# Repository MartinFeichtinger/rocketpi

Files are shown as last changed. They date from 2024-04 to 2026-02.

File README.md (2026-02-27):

# RocketPi
The aim of this project is to controll a water rocket with a Raspberry Pi Zero.

## What is a water rocket?
A water rocket is a type of model rocket using water as its reaction mass.
The water is forced out by a pressurized gas, typically compressed air. Like all rocket engines, it operates on the principle of Newton's third law of motion.



## What's special about our water rocket?
The fuel tank consists of a plastic bottle. This bottle can withstand a maximum pressure of 9 bar.
In order to achieve a higher flight altitude, we have decided to strengthen this plastic bottle with fiber-reinforced tape.
Whith this new tank we are able to reach pressures up to 13 bar.
Futhermore a Raspberry Pi Zero is used to eject the parachute and determine the flight altitude.
The parachute is attached to the top of the water rocket. To eject the parachute, the pre-tensioned handle is opened with three servo motors.
-image of the water rocket

## Rocket launcher


The rocket launcher had already been built beforehand. It also allows the rocket to be filled. Two ball valves can be used to switch between water and compressed air. The water rockets can then be launched by pulling a string.

## Rocketpi


### Raspberry Pi Zero
The Raspberry Pi Zero is a tiny, affordable computer board developed by the Raspberry Pi Foundation. It's small but powerful, with features like a CPU, RAM, storage, and ports for connecting to displays and other devices. It's used for various projects like IoT, robotics, and gaming consoles due to its low cost and versatility.

### BerryIMUv4
IMU stands for Inertial Measurement Unit. It's a device that measures and reports specific forces like acceleration and angular velocity, using a combination of accelerometers, gyroscopes, and sometimes magnetometers. IMUs are commonly used in applications like navigation systems, robotics, virtual reality, and motion tracking. They provide essential data for determining an object's orientation, position, and movement in 3D space.

The BerryIMUv4 is an IMU that was specially developed for the rasberry pi zero. In addition to acceleration, rotation rate and magnetic field, it is possible to measure barometric altitude and temperature. Furthermore, there is a GPS module for position determination.

For more inforations visit: https://ozzmaker.com/product/berrygps-imu/

Example Programms: https://github.com/ozzmaker/BerryIMU

### Power Board
The power board connects the Raspberry Pi to the lithium battery and the servo motors. It also acts as a bridge between the Raspberry Pi and the BerryIMUv4 sensor module, and between the Raspberry Pi and the control panel.

#### Schematic
Screenshot From 2026-02-27 09-51-35

#### PCB layout
Screenshot From 2026-02-27 09-52-22

### Controll Panel
The control panel enables interaction with the Raspberry Pi. On the one hand, control signals can be sent to the Raspberry Pi via a button, and on the other hand, the status of the Raspberry Pi can be displayed via LEDs. The entire system is switched on with a power switch. To signal that the Raspberry Pi is booting, a flashing signal is generated via a 555 timer. Immediately after the boot process, the reset input of the 555 timer is triggered and the boot LED stops flashing and remains lit. 

#### Schematic
Screenshot From 2026-02-27 09-53-32

#### PCB layout
Screenshot From 2026-02-27 09-59-49

## Software
### State-Machine
stateMachine

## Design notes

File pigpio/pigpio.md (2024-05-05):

# pigpio
For all further C programms we will use the `pigpiod_if2.h` library to controll the GPIO-Pins of the Raspberry Pi.
This library allow to control the GPIOs via the socket interface to the pigpio daemon.

To be able to use this library and program the GPIO-Pins, the pigpio package must be installed as explained in the setup guild.

For more informations about pigpio: https://abyz.me.uk/rpi/pigpio/index.html

## GPIO-Pinout
GPIO-Pinout-Diagram-2

## Test program
To test if the pigpio library is installed correctly you can use the `pigpioTest.c` programm.
This programm will toggle the GPIO 17 between HIGH and LOW. 
To make this visible you can use a led with a resistor connected to ground.

- build up the test schematic
- compile the test programm `gcc -Wall -pthread -o pigpioTest pigpioTest.c -lpigpiod_if2 -lrt`
- run the programm with `./pigpioTest`

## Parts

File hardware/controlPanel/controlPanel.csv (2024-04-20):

Source: | /home/martin/Otelo/Elektroniknode/Wasserrakete/Schaltplan/fallschirmsystem_bedienfeld/fallschirmsystem_bedienfeld.kicad_sch
Date: | Fr 09 Dez 2022 00:26:18
Tool: | Eeschema 6.0.9-8da3e8f707~117~ubuntu20.04.1
Generator: | /usr/share/kicad/plugins/bom_csv_grouped_by_value.py
Component Count: | 15
Individual Components:
Item | Qty | Reference(s) | Value | LibPart | Footprint | Datasheet
 |  | C1 | 10u | Device:C | Capacitor_SMD:C_0805_2012Metric_Pad1.18x1.45mm_HandSolder | ~
 |  | D1 | D_Schottky | Device:D_Schottky | Diode_SMD:D_SMA_Handsoldering | ~
 |  | D2 | D_Schottky | Device:D_Schottky | Diode_SMD:D_SMA_Handsoldering | ~
 |  | D3 | Boot_LED | Device:LED | LED_THT:LED_D5.0mm_Horizontal_O1.27mm_Z3.0mm | ~
 |  | D4 | GPS_LED | Device:LED | LED_THT:LED_D5.0mm_Horizontal_O1.27mm_Z3.0mm | ~
 |  | D5 | Network_LED | Device:LED | LED_THT:LED_D5.0mm_Horizontal_O1.27mm_Z3.0mm | ~
 |  | J1 | Power Supply | Connector:Conn_01x02_Female | Connector_Molex:Molex_Micro-Latch_53253-0270_1x02_P2.00mm_Vertical | ~
 |  | J2 | Conn_01x06_Female | Connector:Conn_01x06_Female | Connector_Molex:Molex_KK-254_AE-6410-06A_1x06_P2.54mm_Vertical | ~
 |  | R1 | 10k | Device:R | Resistor_SMD:R_0805_2012Metric_Pad1.20x1.40mm_HandSolder | ~
 |  | R2 | 68k | Device:R | Resistor_SMD:R_0805_2012Metric_Pad1.20x1.40mm_HandSolder | ~
 |  | R3 | 220 | Device:R | Resistor_SMD:R_0805_2012Metric_Pad1.20x1.40mm_HandSolder | ~
 |  | R4 | 680 | Device:R | Resistor_SMD:R_0805_2012Metric_Pad1.20x1.40mm_HandSolder | ~
 |  | R5 | 220 | Device:R | Resistor_SMD:R_0805_2012Metric_Pad1.20x1.40mm_HandSolder | ~
 |  | SW1 | Ein/Aus | Switch:SW_Push_SPDT | footprints:slide_switch | ~
 |  | U1 | LM555xM | Timer:LM555xM | Package_DIP:DIP-8_W7.62mm_Socket_LongPads | http://www.ti.com/lit/ds/symlink/lm555.pdf
Collated Components:
Item | Qty | Reference(s) | Value | LibPart | Footprint | Datasheet
1 | 1 | C1 | 10u | Device:C | Capacitor_SMD:C_0805_2012Metric_Pad1.18x1.45mm_HandSolder | ~
2 | 2 | D1, D2 | D_Schottky | Device:D_Schottky | Diode_SMD:D_SMA_Handsoldering | ~
3 | 1 | D3 | Boot_LED | Device:LED | LED_THT:LED_D5.0mm_Horizontal_O1.27mm_Z3.0mm | ~
4 | 1 | D4 | GPS_LED | Device:LED | LED_THT:LED_D5.0mm_Horizontal_O1.27mm_Z3.0mm | ~
5 | 1 | D5 | Network_LED | Device:LED | LED_THT:LED_D5.0mm_Horizontal_O1.27mm_Z3.0mm | ~
6 | 1 | J1 | Power Supply | Connector:Conn_01x02_Female | Connector_Molex:Molex_Micro-Latch_53253-0270_1x02_P2.00mm_Vertical | ~
7 | 1 | J2 | Conn_01x06_Female | Connector:Conn_01x06_Female | Connector_Molex:Molex_KK-254_AE-6410-06A_1x06_P2.54mm_Vertical | ~
8 | 1 | R1 | 10k | Device:R | Resistor_SMD:R_0805_2012Metric_Pad1.20x1.40mm_HandSolder | ~
9 | 1 | R2 | 68k | Device:R | Resistor_SMD:R_0805_2012Metric_Pad1.20x1.40mm_HandSolder | ~
10 | 2 | R3, R5 | 220 | Device:R | Resistor_SMD:R_0805_2012Metric_Pad1.20x1.40mm_HandSolder | ~
11 | 1 | R4 | 680 | Device:R | Resistor_SMD:R_0805_2012Metric_Pad1.20x1.40mm_HandSolder | ~
12 | 1 | SW1 | Ein/Aus | Switch:SW_Push_SPDT | footprints:slide_switch | ~
13 | 1 | U1 | LM555xM | Timer:LM555xM | Package_DIP:DIP-8_W7.62mm_Socket_LongPads | http://www.ti.com/lit/ds/symlink/lm555.pdf

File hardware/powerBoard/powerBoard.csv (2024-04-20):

Source: | /home/martin/Otelo/Elektroniknode/Wasserrakete/Schaltplan/power_board/power_board.kicad_sch
Date: | Sa 12 Aug 2023 21:56:18
Tool: | Eeschema 6.0.10-86aedd382b~118~ubuntu22.10.1
Generator: | /usr/share/kicad/plugins/bom_csv_grouped_by_value_with_fp.py
Component Count: | 25
Ref | Qnty | Value | Cmp name | Footprint | Description | Vendor
C1, C2, | 2 | 100nF | C | Capacitor_SMD:C_0805_2012Metric_Pad1.18x1.45mm_HandSolder | Unpolarized capacitor
C3, C4, C5, C6, C7, C8, | 6 | 10u | C | Capacitor_SMD:C_0805_2012Metric_Pad1.18x1.45mm_HandSolder | Unpolarized capacitor
J1, | 1 | Batt | Conn_01x02_Female | MyFootprints:Pfusch_Conn | Generic connector, single row, 01x02, script generated (kicad-library-utils/schlib/autogen/connector/)
J2, | 1 | Berry IMU | Conn_02x05_Odd_Even | Connector_PinSocket_2.54mm:PinSocket_2x05_P2.54mm_Vertical | Generic connector, double row, 02x05, odd/even pin numbering scheme (row 1 odd numbers, row 2 even numbers), script generated (kicad-library-utils/schlib/autogen/connector/)
J3, | 1 | Control_Panel | Conn_02x04_Top_Bottom | Connector_PinHeader_2.54mm:PinHeader_2x04_P2.54mm_Vertical | Generic connector, double row, 02x04, top/bottom pin numbering scheme (row 1: 1...pins_per_row, row2: pins_per_row+1 ... num_pins), script generated (kicad-library-utils/schlib/autogen/connector/)
J4, | 1 | Servo_1 | Conn_01x02_Female | MyFootprints:Pfusch_Conn | Generic connector, single row, 01x02, script generated (kicad-library-utils/schlib/autogen/connector/)
J5, | 1 | Servo_2 | Conn_01x02_Female | MyFootprints:Pfusch_Conn | Generic connector, single row, 01x02, script generated (kicad-library-utils/schlib/autogen/connector/)
J6, | 1 | Servo_3 | Conn_01x02_Female | MyFootprints:Pfusch_Conn | Generic connector, single row, 01x02, script generated (kicad-library-utils/schlib/autogen/connector/)
J7, | 1 | Raspi | Conn_02x05_Odd_Even | Connector_PinSocket_2.54mm:PinSocket_2x05_P2.54mm_Vertical | Generic connector, double row, 02x05, odd/even pin numbering scheme (row 1 odd numbers, row 2 even numbers), script generated (kicad-library-utils/schlib/autogen/connector/)
J8, | 1 | Masse | Conn_01x02_Male | Connector_PinHeader_2.54mm:PinHeader_1x02_P2.54mm_Vertical | Generic connector, single row, 01x02, script generated (kicad-library-utils/schlib/autogen/connector/)
R1, R2, R3, | 3 | 10k | R | Resistor_SMD:R_0805_2012Metric_Pad1.20x1.40mm_HandSolder | Resistor
R4, R5, | 2 | 4,7k | R | Resistor_SMD:R_0805_2012Metric_Pad1.20x1.40mm_HandSolder | Resistor
R6, R7, | 2 | R | R | Resistor_SMD:R_0805_2012Metric_Pad1.20x1.40mm_HandSolder | Resistor
U1, | 1 | R-78C5.0-1.0 | R-78C5.0-1.0 | Converter_DCDC:Converter_DCDC_RECOM_R-78E-0.5_THT | 1A Step-Down DC/DC-Regulator, 7-42V input, 5V fixed Output Voltage, LM78xx replacement, -40°C to +85°C, SIP3
U2, | 1 | DRV8801PWP | DRV8801PWP | Package_SO:HTSSOP-16-1EP_4.4x5mm_P0.65mm_EP3.4x5mm_Mask3x3mm_ThermalVias | H-Bridge Motor Driver, TSSOP-16

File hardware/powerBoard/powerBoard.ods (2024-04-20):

Component Count: | 25
Ref | Qnty | Value
C1, C2, | 2 | 100nF
C3, C4, C5, C6, C7, C8, | 6 | 10u
J1, | 1 | Batt
J2, | 1 | Berry IMU
J3, | 1 | Control_Panel
J4, | 1 | Servo_1
J5, | 1 | Servo_2
J6, | 1 | Servo_3
J7, | 1 | Raspi
J8, | 1 | Masse
R1, R2, R3, | 3 | 10k
R4, R5, | 2 | 4,7k
R6, R7, | 2 | R
U1, | 1 | R-78C5.0-1.0
U2, | 1 | DRV8801PWP

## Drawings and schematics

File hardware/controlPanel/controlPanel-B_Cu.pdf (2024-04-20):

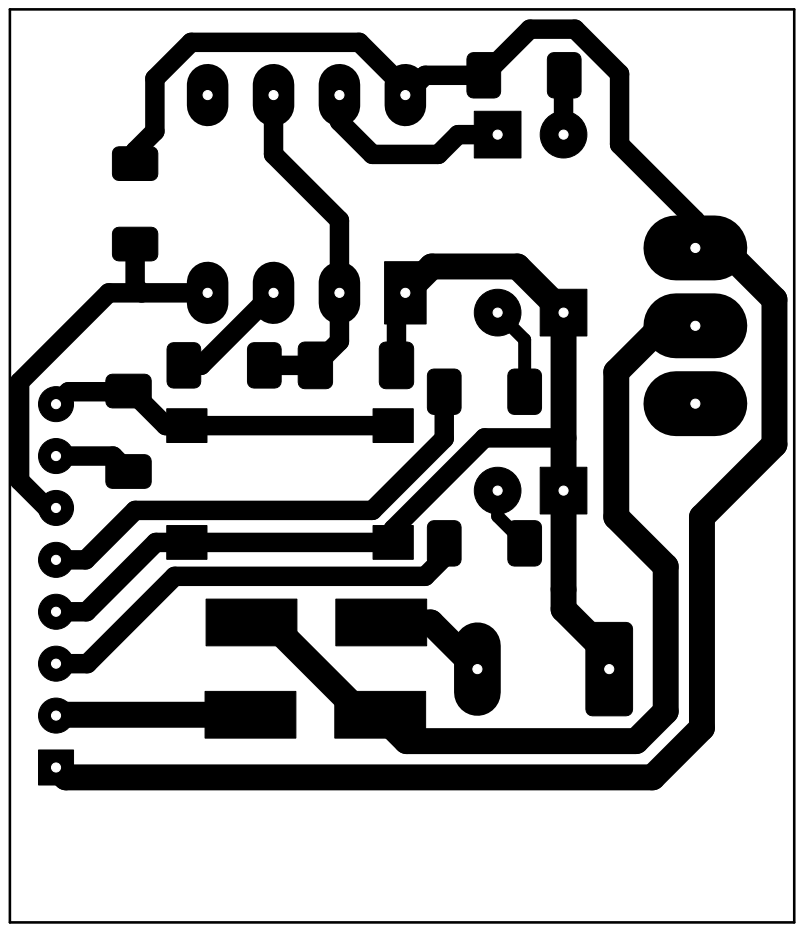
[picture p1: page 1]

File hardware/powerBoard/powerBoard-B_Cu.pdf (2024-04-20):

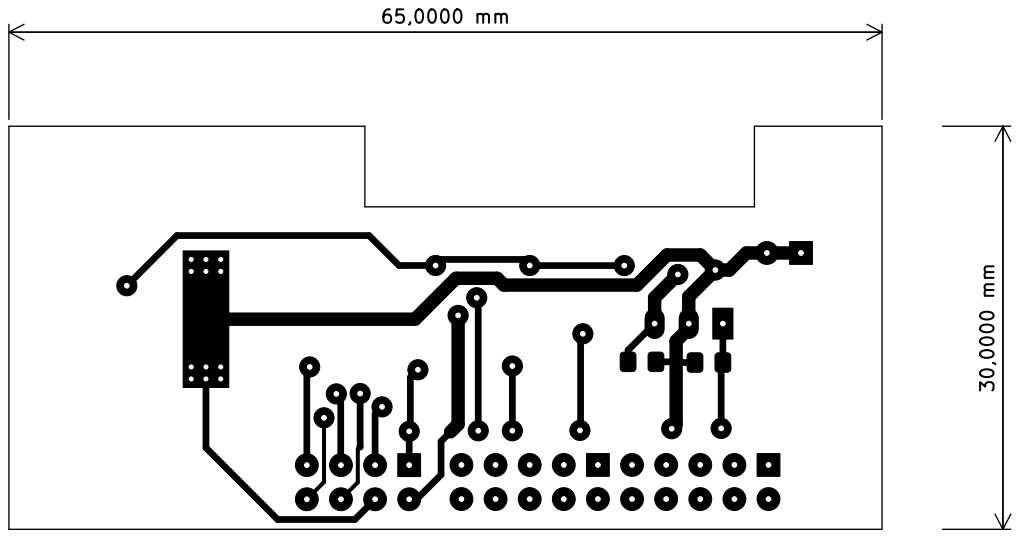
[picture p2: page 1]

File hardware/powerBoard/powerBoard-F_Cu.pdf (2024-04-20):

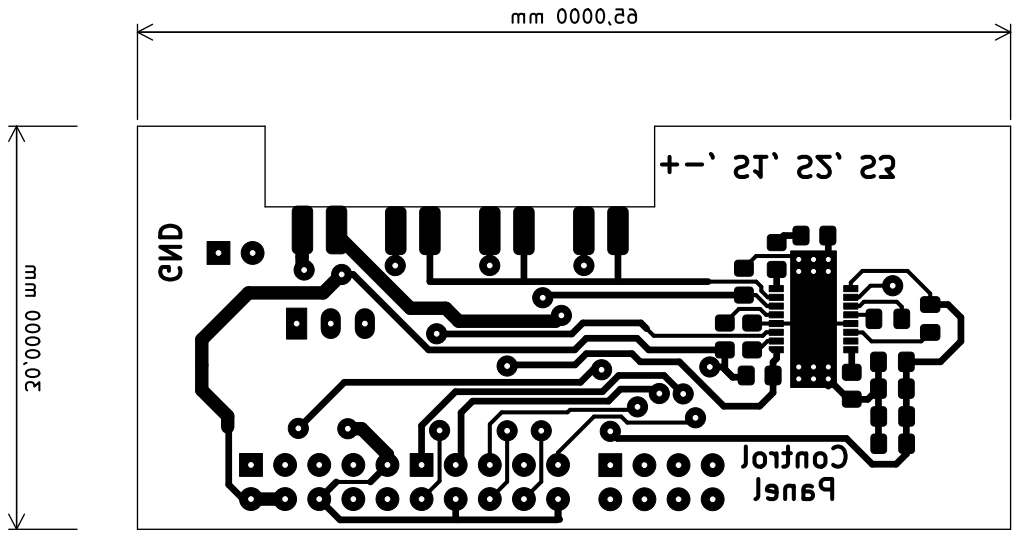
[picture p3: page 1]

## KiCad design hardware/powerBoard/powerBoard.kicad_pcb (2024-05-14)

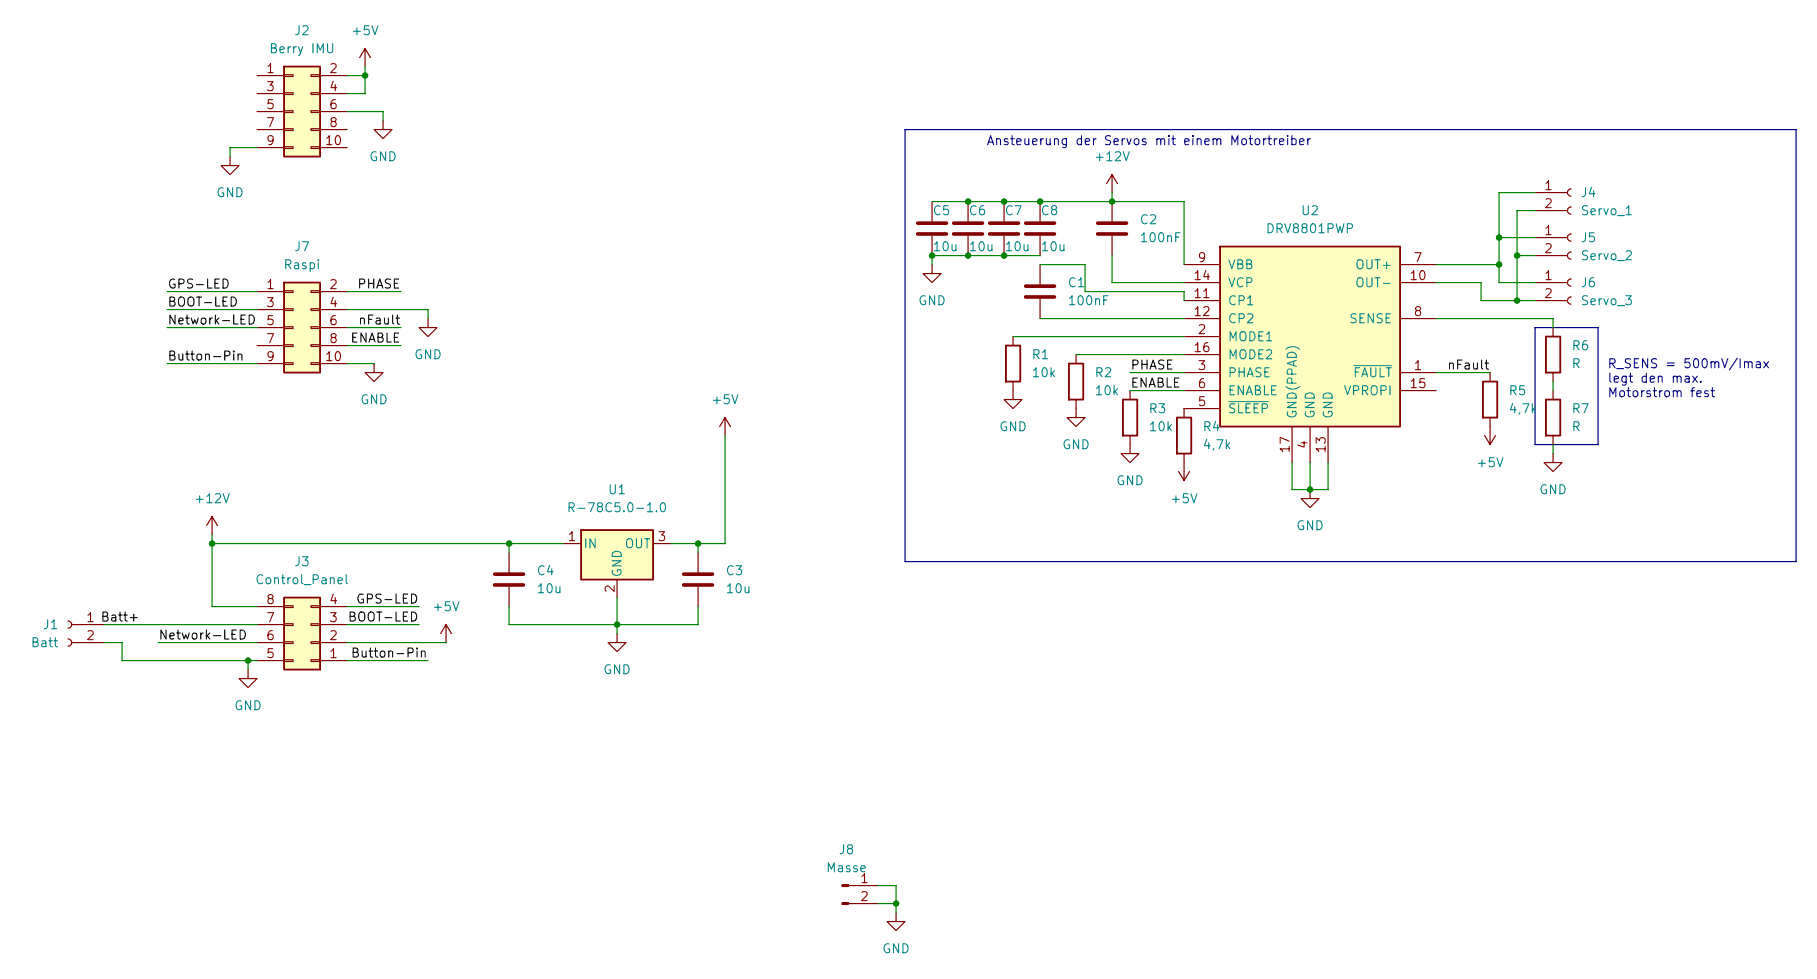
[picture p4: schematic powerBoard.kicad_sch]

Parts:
C1, C2: 100nF; C_0805_2012Metric_Pad1.18x1.45mm_HandSolder
C3, C4, C5, C6, C7, C8: 10u; C_0805_2012Metric_Pad1.18x1.45mm_HandSolder
J1: Batt; Pfusch_Conn
J2: Berry IMU; PinSocket_2x05_P2.54mm_Vertical
J3: Control_Panel; IDC-Header_2x04_P2.54mm_Vertical
J4: Servo_1; Pfusch_Conn
J5: Servo_2; Pfusch_Conn
J6: Servo_3; Pfusch_Conn
J7: Raspi; PinSocket_2x05_P2.54mm_Vertical
J8: Masse; PinHeader_1x02_P2.54mm_Vertical
R1, R2, R3: 10k; R_0805_2012Metric_Pad1.20x1.40mm_HandSolder
R4, R5: 4,7k; R_0805_2012Metric_Pad1.20x1.40mm_HandSolder
R6, R7: R; R_0805_2012Metric_Pad1.20x1.40mm_HandSolder
U1: R-78C5.0-1.0; Converter_DCDC_RECOM_R-78E-0.5_THT
U2: DRV8801PWP; HTSSOP-16-1EP_4.4x5mm_P0.65mm_EP3.4x5mm_Mask3x3mm_ThermalVi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

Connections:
+5V: C3.1, J2.2, J2.4, J3.2, R4.2, R5.2, U1.3 (OUT); also elsewhere on the board
+12V: C2.1, C4.1, C5.1, C6.1, C7.1, C8.1, J3.8, U1.1 (IN), U2.9 (VBB)
/BOOT-LED: J3.3, J7.3
/Batt+: J1.1, J3.7
/Button-Pin: J3.1, J7.9
/ENABLE: J7.8, R3.1, U2.6 (ENABLE)
/GPS-LED: J3.4, J7.1
/Network-LED: J3.6, J7.5
/PHASE: J7.2, U2.3 (PHASE)
/nFault: J7.6, R5.1, U2.1 (~FAULT)
GND: C3.2, C4.2, C5.2, C6.2, C7.2, C8.2, J1.2, J2.6, J2.9, J3.5, J7.4, J7.10, J8.1, J8.2, R1.2, R2.2, R3.2, R7.2, U1.2 (GND), U2.4 (GND), U2.13 (GND), U2.17 (GND(PPAD)); also elsewhere on the board
unnamed: C1.1, U2.11 (CP1)
unnamed: C1.2, U2.12 (CP2)
unnamed: C2.2, U2.14 (VCP)
unnamed: J4.1, J5.1, J6.1, U2.7 (OUT+)
unnamed: J4.2, J5.2, J6.2, U2.10 (OUT-)
unnamed: R1.1, U2.2 (MODE1)
unnamed: R2.1, U2.16 (MODE2)
unnamed: R4.1, U2.5 (~SLEEP)
unnamed: R6.1, U2.8 (SENSE)
unnamed: R6.2, R7.1

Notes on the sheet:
R_SENS = 500mV/Imax legt den max. Motorstrom fest
Ansteuerung der Servos mit einem Motortreiber

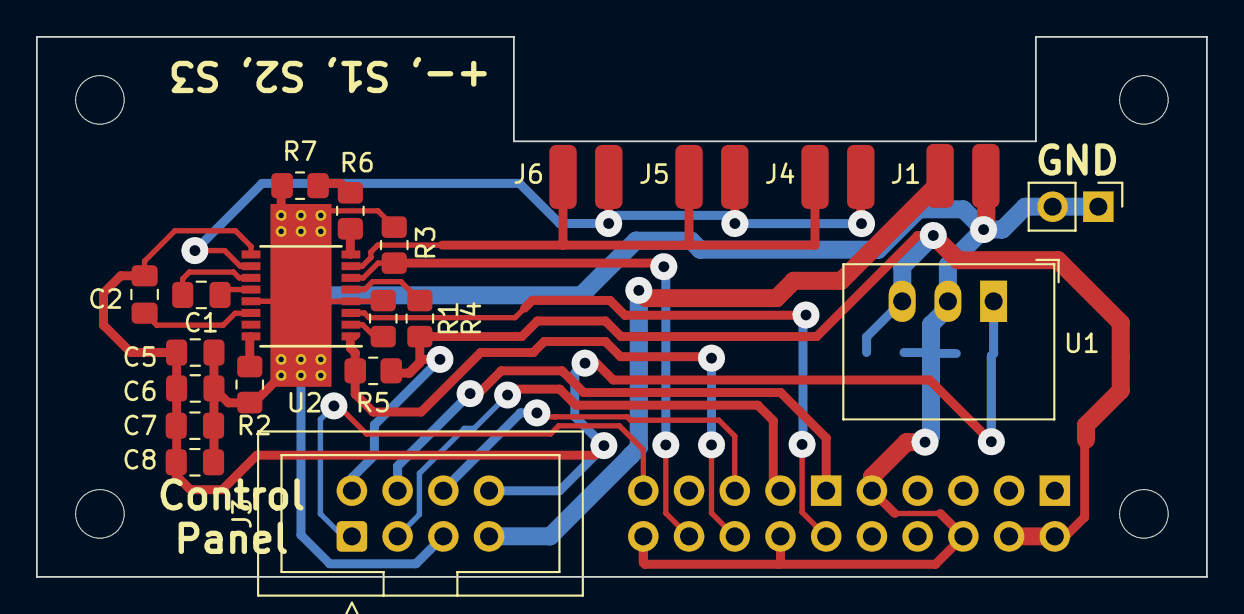
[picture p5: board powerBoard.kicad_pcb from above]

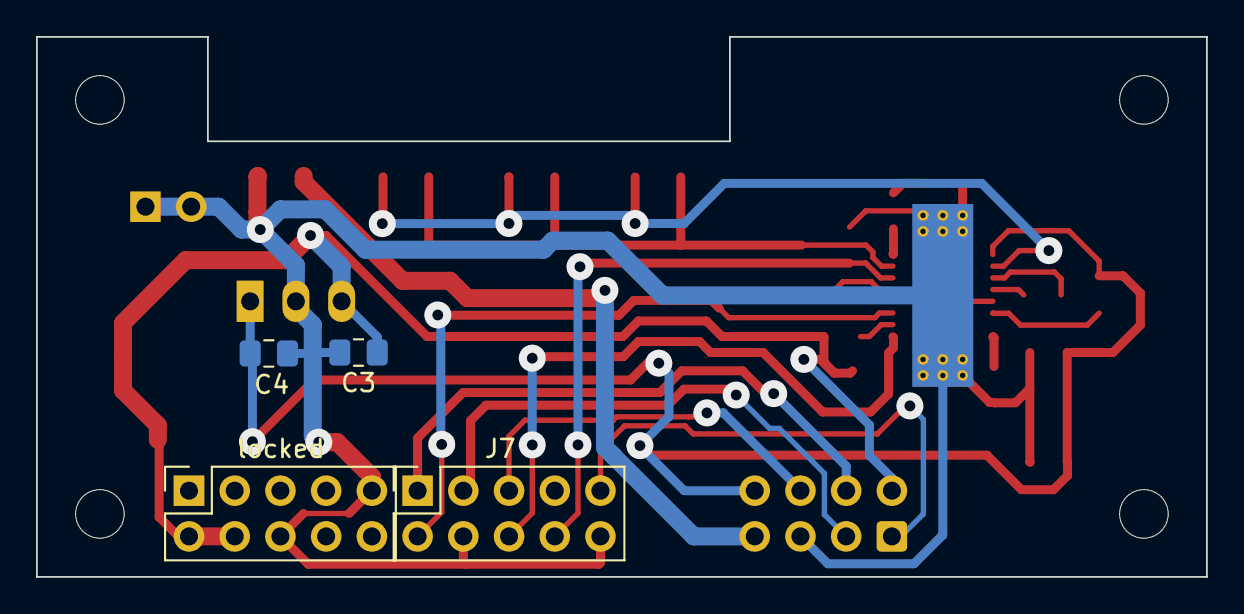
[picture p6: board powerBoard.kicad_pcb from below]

Board: 2 copper layers, 65.0 x 30.0 mm, 25 parts (4 on the bottom side), 21 nets.

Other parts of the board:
locked: Berry IMU; PinSocket_2x05_P2.54mm_Vertical

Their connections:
+5V: locked.2, locked.4; also elsewhere on the board
GND: locked.6, locked.9; also elsewhere on the board

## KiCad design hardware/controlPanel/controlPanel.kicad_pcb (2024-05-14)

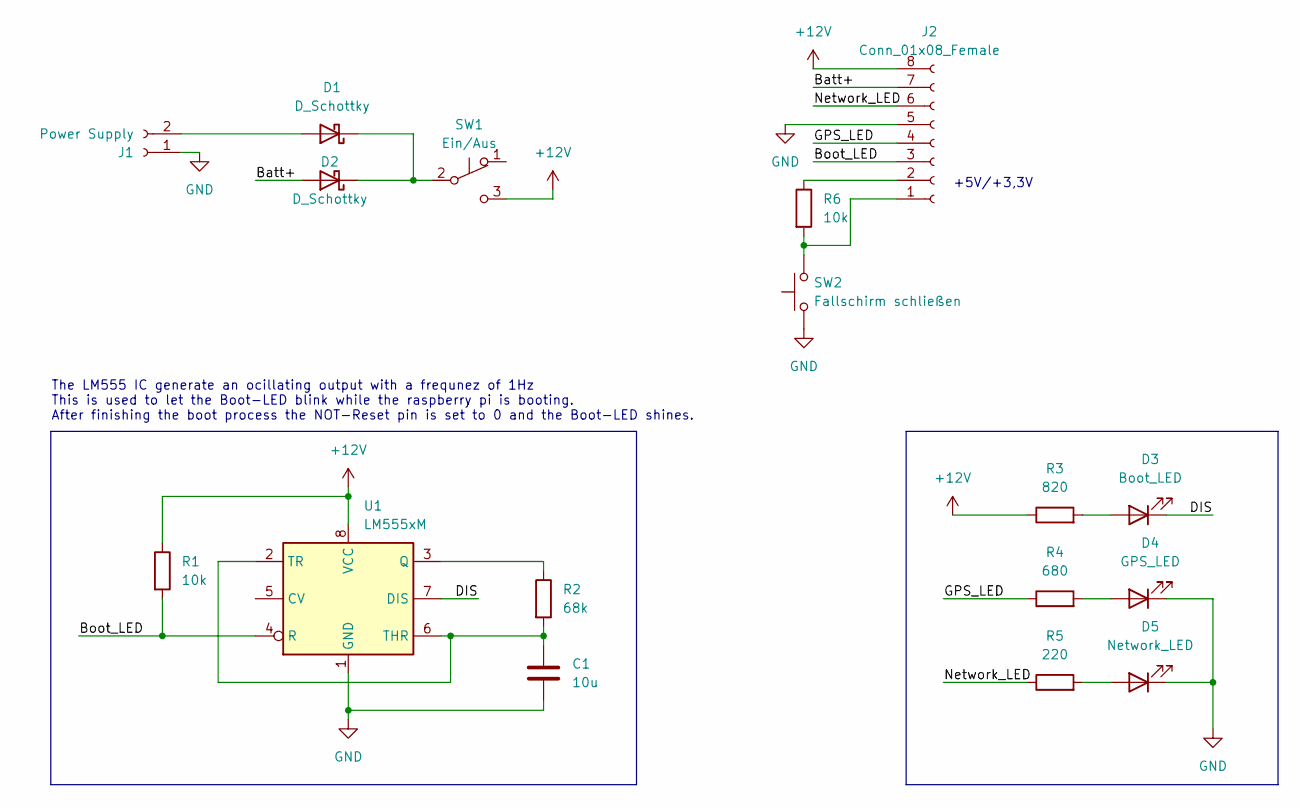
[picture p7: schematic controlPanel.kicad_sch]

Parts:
C1: 10u; C_1206_3216Metric_Pad1.33x1.80mm_HandSolder
D1, D2: D_Schottky; D_SMA_Handsoldering
D3: Boot_LED; LED_D3.0mm
D4: GPS_LED; LED_D3.0mm
D5: Network_LED; LED_D3.0mm
J1: Power Supply; PhoenixContact_MCV_1,5_2-G-5.08_1x02_P5.08mm_Vertical
J2: Conn_01x08_Female; PinHeader_1x08_P2.00mm_Vertical
R1, R6: 10k; R_1206_3216Metric_Pad1.30x1.75mm_HandSolder
R2: 68k; R_1206_3216Metric_Pad1.30x1.75mm_HandSolder
R3: 820; R_1206_3216Metric_Pad1.30x1.75mm_HandSolder
R4: 680; R_1206_3216Metric_Pad1.30x1.75mm_HandSolder
R5: 220; R_1206_3216Metric_Pad1.30x1.75mm_HandSolder
SW1: Ein/Aus; slide_switch
SW2: Fallschirm schließen; SW_Push_1P1T_NO_6x6mm_H9.5mm
U1: LM555xM; DIP-8_W7.62mm_Socket_LongPads

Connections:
+12V: J2.8, R1.1, R3.1, SW1.3 (C), U1.8 (VCC)
/Batt+: D2.2 (A), J2.7
/Boot_LED: J2.3, R1.2, U1.4 (R)
/DIS: D3.1 (K), U1.7 (DIS)
/GPS_LED: J2.4, R4.1
/Network_LED: J2.6, R5.1
GND: C1.2, D4.1 (K), D5.1 (K), J1.1, J2.5, SW2.1, U1.1 (GND)
unnamed: C1.1, R2.2, U1.2 (TR), U1.6 (THR)
unnamed: D1.1 (K), D2.1 (K), SW1.2 (B)
unnamed: D1.2 (A), J1.2
unnamed: D3.2 (A), R3.2
unnamed: D4.2 (A), R4.2
unnamed: D5.2 (A), R5.2
unnamed: J2.1, R6.2, SW2.2
unnamed: J2.2, R6.1
unnamed: R2.1, U1.3 (Q)

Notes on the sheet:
+5V/+3,3V
The LM555 IC generate an ocillating output with a frequnez of 1Hz This is used to let the Boot-LED blink while the raspberry pi is booting. After finishing the boot process the NOT-Reset pin is set to 0 and the Boot-LED shines.

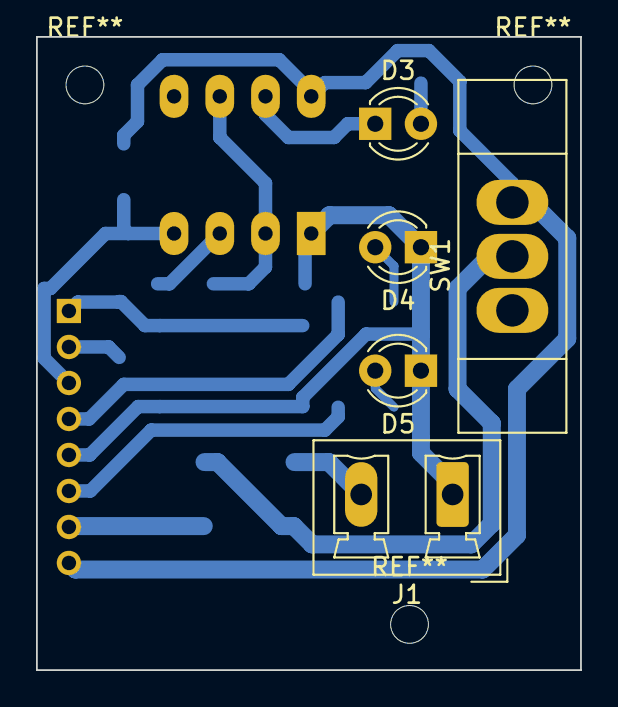
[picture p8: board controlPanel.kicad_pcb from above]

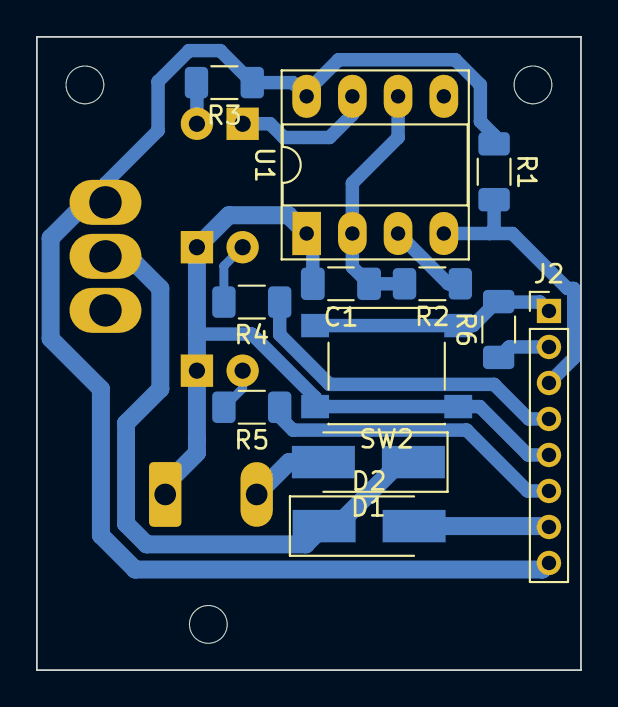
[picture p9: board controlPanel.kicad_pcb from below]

Board: 2 copper layers, 30.2 x 35.2 mm, 17 parts (12 on the bottom side), 16 nets.

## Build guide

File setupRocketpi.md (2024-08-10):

# Setup your Rocketpi
This projekt is developed for a **Raspberry Pi Zero 2W**. You can also use an Raspberry Pi Zero W but the *Remote Development Extenion* for VS-Code won't work.

## Prepare Raspberry Pi
- install the Raspberry Pi imager (`sudo apt install rpi-imager`)
- insert your microSD-Card (at least 8GB)
- open and choose **Raspberry Pi OS Lite (64-Bit)** for the **Raspberry Pi Zero 2W** (32-Bit  for Raspberry Pi Zero W)
- select your microSD-Card and write your image

## First Boot
- insert your microSD-Card in your Raspberry Zero 2W
- connect the Raspberry Pi to a monitor, a keyboard and powersupply and let him boot
- open the `raspi-config` and change hostname to `rocketpi-xx`  
- and activate `ssh`
- activate wlan (mobile HotSpot rescommended) and reboot
- (the order of this settings are important)

## Further configurations
- connect to the Raspi via ssh (`ssh pi@rocketpi-xx.local`) 
- open `raspi-config` and activate `i2c` and `Serial`
- change the time zone to your local time. (you can check the time with the comand `date`)
- close `raspi-config` and reboot

## Clone Rocketpi-Projekt
- install git: `sudo apt install git`
- `git clone https://github.com/MartinFeichtinger/rocketpi`
- bei Änderungen mit `git commit` und `git push` hochladen (username and token erforderlich)

## Configurations for the GPIO-Programming
- install the pigpio library `sudo apt install pigpio`
- setup the pigpio daemon to start at boot `sudo systemctl enable pigpiod`
- test the configuration with the `pigpioTest.c` program (located under pigpio) 

## Configurate VS-Code
- install vs-code on your ubuntu system
- install the **C/C++** extention
- install the **Remote Development** extention

## Programm Boot-LED
- `sudo nano /etc/rc.local`
- insert this two lines befor the `exit(0)`
- `/usr/bin/pigs m 27 w`
- `/usr/bin/pigs w 27 0`

## Configurate files to be used by pigpio
- generate folder for the files
- add the folder to the pigpio access file (`sudo nano /opt/pigpio/access` and add `/dir/* u`)
- use the whole file path to open the file in your program

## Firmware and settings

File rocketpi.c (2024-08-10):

#include <stdio.h>
#include <stdbool.h>
#include <stdlib.h>
#include <string.h>
#include <math.h>
#include <pigpiod_if2.h>
#include <signal.h>

// file paths
#define OUTPUT_FOLDER	"/home/pi/rocketpi/measurements/"

// powerBoard
#define ENABLE			24
#define PHASE			18

// controlPanel
#define ARMED_LED		22		// NET_LED on the schematic
#define LOADED_LED		17		// GPS_LED on the schematic
#define BUTTON			10

// MPU6050
#define MPU6050_ADRESS	0x68

// global variables
int pi;
int i2c_handle;
int file_handle;

enum State {OPEN, SHAKING, CLOSING, LOADED, ARMED, UNARMED, OPENING, FLYING, FLYING_OPEN};
enum State state = OPEN;

uint32_t last_rising_tick;
bool button_pressed;

uint32_t timer_start;

bool saveMeasurements = false;
uint32_t timestamp;
int flyingState=0;
int16_t accX, accY, accZ, gyrX, gyrY, gyrZ, tVal;
int16_t acc;
double temp = 0.0;

// function prototypes
bool init();
bool generateNewFile();
void sigintlHandler(int signal);
void readMPU6050();
void button_cb(int pi, unsigned user_gpio, unsigned edge, uint32_t tick);


int main(){
	signal(SIGINT, sigintlHandler); // this handler is called when ctrl+c is pressed

	if(init() == false){
		return -1;
	}

	while(true){
		switch(state){
			case OPEN:
				// wait for button press
				break;

			case SHAKING:
				set_PWM_dutycycle(pi, ENABLE, 10);
				gpio_write(pi, PHASE, 0);
				time_sleep(0.07);
				gpio_write(pi, PHASE, 1);
				time_sleep(0.07);
				// do this until the button get released
				break;

			case CLOSING:
				gpio_write(pi, PHASE, 0);
				set_PWM_dutycycle(pi, ENABLE, 10);
				time_sleep(1);
				set_PWM_dutycycle(pi, ENABLE, 0);

				gpio_write(pi, LOADED_LED, 1);
				state = LOADED;
				break;

			case LOADED:
				if(button_pressed){
					uint32_t duration = (get_current_tick(pi) - last_rising_tick)/1000; 	// milliseconds
					if(duration >= 2000){
						button_pressed = false;

						gpio_write(pi, ARMED_LED, 1);
						generateNewFile();
						saveMeasurements=true;
						state = ARMED;
					}
				}
				break;

			case ARMED:
				if(button_pressed){
					uint32_t duration = (get_current_tick(pi) - last_rising_tick)/1000; 	// milliseconds
					if(duration >= 2000){
						button_pressed = false;

						gpio_write(pi, ARMED_LED, 0);
						saveMeasurements=false;
						file_close(pi, file_handle);
						printf("rocketpi unarmed\n\n");
						state = UNARMED;
					}
				}

				// if accelerations is detected
				if(acc >= 2*9810){
					timer_start = get_current_tick(pi);
					flyingState=1;
					state = FLYING;
				}
				break;

			case UNARMED:
				// wait for button press to switch to OPENING
				break;

			case OPENING:
				gpio_write(pi, PHASE, 1);
				set_PWM_dutycycle(pi, ENABLE, 10);
				time_sleep(1);
				set_PWM_dutycycle(pi, ENABLE, 0);

				gpio_write(pi, LOADED_LED, 0);
				state = OPEN;
				break;

			case FLYING:
				if(get_current_tick(pi) >= timer_start + 2000*1000){
					timer_start = get_current_tick(pi);
					flyingState=2;
					state = FLYING_OPEN;
				}
				break;

			case FLYING_OPEN:
				if(get_current_tick(pi) < timer_start + 1000*1000){
	                                // opening parachute
	                                gpio_write(pi, PHASE, 1);
	                                set_PWM_dutycycle(pi, ENABLE, 10);
				}
				else{
                                        set_PWM_dutycycle(pi, ENABLE, 0);
                                        gpio_write(pi, LOADED_LED, 0);
                                        flyingState=3;
				}

				if(get_current_tick(pi) >= timer_start + 15000*1000){
					gpio_write(pi, ARMED_LED, 0);
					saveMeasurements=false;
					flyingState=0;
					file_close(pi, file_handle);
					printf("Parachute opened\n\n");
					state = OPEN;
				}
				break;
		}

		if(saveMeasurements){
		timestamp=get_current_tick(pi)/1000;
		char str[300];
		readMPU6050(pi, i2c_handle);
		sprintf(str, "%d	%d	%d	%d	%d	%d	%d	%d	%d	%.2f\n", timestamp, flyingState, acc, accX, accY, accZ, gyrX, gyrY, gyrZ, temp);
		printf(str);

		int i=0;
		while(str[i] != '\0'){
			i++;
		}

		if(file_write(pi, file_handle, str, i) == 0){
			//printf("Stored to file sucessfully\n");
		}
		else{
			printf("Unable to save to file\n");
		}
	}

	time_sleep(0.05);
	}
}


bool init(){
	// init gpio client
	pi = pigpio_start(NULL, NULL);
	if(pi < 0){
		printf("Raspberry Pi not found");
		return -1;
	}

	// init gpios
	set_mode(pi, ENABLE, PI_OUTPUT);
	set_mode(pi, PHASE, PI_OUTPUT);

	set_mode(pi, ARMED_LED, PI_OUTPUT);
	set_mode(pi, LOADED_LED, PI_OUTPUT);
	set_mode(pi, BUTTON, PI_INPUT);

	gpio_write(pi, ARMED_LED, 0);
	gpio_write(pi, LOADED_LED, 0);

	// cofigurate the pwm
	int pwm_frequency = 8000;
	int real_pwm_frequency = set_PWM_frequency(pi, ENABLE, pwm_frequency);
	printf("pwm_frequency: set=%d; real=%d\n", pwm_frequency, real_pwm_frequency);

	int pwm_range = 25;
	int real_pwm_range = set_PWM_range(pi, ENABLE, pwm_range);
	printf("pwm_range: set=%d; real=%d\n", pwm_range, real_pwm_range);

	// init button spefic gpio settings
	set_glitch_filter(pi, BUTTON, 20000);	// ingor all input changes for 20ms after the input state changes
	const int cb_id = callback(pi, BUTTON, EITHER_EDGE, button_cb);
	if(cb_id < 0){
		printf("init callback failed");
		return -1;
	}
	
	// init i2c
	i2c_handle = i2c_open(pi, 1, MPU6050_ADRESS, 0);
	if(i2c_handle < 0){
		printf("i2c device not found\n");
		return false;
	}

	// init mpu6050
	i2c_write_byte_data(pi, i2c_handle, 0x6B, 0x00);	// wake up mpu6050
	i2c_write_byte_data(pi, i2c_handle, 0x1B, 0x08);	// set full scale range of gyroscope to +-500°/s
	i2c_write_byte_data(pi, i2c_handle, 0x1C, 0x08);	// set full scale range of accelerometer to +-4g
	//i2c_write_byte_data(pi, i2c_handle, 0x19, 0x07);	// set sample rate to 1kHz
	i2c_write_byte_data(pi, i2c_handle, 0x1A, 0x00);	// set digital low pass filter to 260Hz
	i2c_write_byte_data(pi, i2c_handle, 0x6C, 0x00);	// disable sleep mode

	return true;
}

bool generateNewFile(){
	char searchString[] = OUTPUT_FOLDER "mpu6050-*.txt";
	char files[1000];
	int c = file_list(pi, searchString, files, sizeof(files));

	char filename[20];
	if(c >= 0){
		files[c]=0;

		int numberOfFiles=0;
		for(int i=0; i<c; i++){
			if(files[i] == '\n'){
				numberOfFiles++;
			}
		}
		sprintf(filename, "mpu6050-%.2d.txt", numberOfFiles);
	}
	else{
		strcpy(filename, "mpu6050-00.txt");
	}

	char outputFile[] = OUTPUT_FOLDER;
	strcat(outputFile, filename);
	printf("output file: %s\n", outputFile);

	char command[100];
	sprintf(command, "touch %s", outputFile);
	system(command);

	file_handle = file_open(pi, outputFile, PI_FILE_WRITE);
	if(file_handle >= 0){
		printf("File opend succesfully\n\n");
		char init_headline[] = {"time	state	acc	accX	accY	accZ	gyrX	gyrY	gyrZ	temp\n"};

		if(file_write(pi, file_handle, init_headline, sizeof(init_headline)-1) == 0){
			printf(init_headline);
		}
		else{
			printf("Unable to save to file\n");
			return false;
		}
	}
	else{
		printf(pigpio_error(file_handle));
		return false;
	}

	return true;
}

void readMPU6050(){
	// read accelerometer values
	i2c_write_byte_data(pi, i2c_handle, 0x3B, 0x00);
	accX = i2c_read_byte_data(pi, i2c_handle, 0x3B) << 8 | i2c_read_byte_data(pi, i2c_handle, 0x3C);
	accY = i2c_read_byte_data(pi, i2c_handle, 0x3D) << 8 | i2c_read_byte_data(pi, i2c_handle, 0x3E);
	accZ = i2c_read_byte_data(pi, i2c_handle, 0x3F) << 8 | i2c_read_byte_data(pi, i2c_handle, 0x40);
	acc = sqrt(accX*accX + accY*accY + accZ*accZ);
	
	// read gyroscope values
	gyrX = i2c_read_byte_data(pi, i2c_handle, 0x43) << 8 | i2c_read_byte_data(pi, i2c_handle, 0x44);
	gyrY = i2c_read_byte_data(pi, i2c_handle, 0x45) << 8 | i2c_read_byte_data(pi, i2c_handle, 0x46);
	gyrZ = i2c_read_byte_data(pi, i2c_handle, 0x47) << 8 | i2c_read_byte_data(pi, i2c_handle, 0x48);
	
	// read temperature value
	tVal = i2c_read_byte_data(pi, i2c_handle, 0x41) << 8 | i2c_read_byte_data(pi, i2c_handle, 0x42);
	temp = (double)tVal / 340.0 + 36.53;
}

void button_cb(int pi, unsigned user_gpio, unsigned edge, uint32_t tick){
	if(edge == RISING_EDGE){
		if(state == OPEN){
			state = SHAKING;
		}
		else if(state == LOADED || state == ARMED){
			last_rising_tick = tick;
			button_pressed = true;
		}
		else if(state == UNARMED){
			state = OPENING;
		}
	}
	else if(edge == FALLING_EDGE){
		if(state == SHAKING){
			state = CLOSING;
		}
	}
}

void sigintlHandler(int signal){
	printf("\n\nProgramm interupted (ctrl+c)\n");
	printf("i2c_handler stopped\n");
	printf("file closed\n");
	i2c_close(pi, i2c_handle);
	file_close(pi, file_handle);
	exit(0);
}

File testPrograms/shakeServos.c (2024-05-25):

#include <stdio.h>
#include <stdbool.h>
#include <pigpiod_if2.h>

// powerBoard
#define ENABLE		24
#define PHASE		18
#define NFAULT		23

// controlPanel
#define GPS_LED		17
#define BOOT_LED	27
#define NET_LED		22
#define BUTTON		10


void nfault_cb(int pi, unsigned user_gpio, unsigned edge, uint32_t tick);
void button_cb(int pi, unsigned user_gpio, unsigned edge, uint32_t tick);

bool shaking=false;

int main(){
	////////////////////////// INIT GPIO SETTINGS //////////////////////////
	// init gpio client
	const int pi = pigpio_start(NULL, NULL);
	if(pi < 0){
		printf("Raspberry Pi not found");
		return -1;
	}

	// init gpios
	set_mode(pi, ENABLE, PI_OUTPUT);
	set_mode(pi, PHASE, PI_OUTPUT);
	set_mode(pi, NFAULT, PI_INPUT);

	set_mode(pi, GPS_LED, PI_OUTPUT);
	set_mode(pi, BOOT_LED, PI_OUTPUT);
	set_mode(pi, NET_LED, PI_OUTPUT);
	set_mode(pi, BUTTON, PI_INPUT);

	// init button spefic gpio settings
	set_glitch_filter(pi, BUTTON, 20000);	// ingor all input changes for 20ms after the input state changes
	const int cb_id = callback(pi, BUTTON, EITHER_EDGE, button_cb);
	if(cb_id < 0){
		printf("init callback failed");
		return -1;
	}

	// cofigurate the pwm
	int pwm_frequency = 8000;
	int real_pwm_frequency = set_PWM_frequency(pi, ENABLE, pwm_frequency);
	printf("pwm_frequency: set=%d; real=%d\n", pwm_frequency, real_pwm_frequency);

	int pwm_range = 25;
	int real_pwm_range = set_PWM_range(pi, ENABLE, pwm_range);	// => 1 = 1%
	printf("pwm_range: set=%d; real=%d\n", pwm_range, real_pwm_range);

	// init NFAULT callback function
	const int nfault_cb_id = callback(pi, NFAULT, EITHER_EDGE, nfault_cb);
	if(nfault_cb_id < 0){
		printf("init callback failed");
		return -1;
	}

	////////////////////////// START OF THE REAL SHIT //////////////////////////
	gpio_write(pi, BOOT_LED, 0);

	while(1){
		if(shaking){
			set_PWM_dutycycle(pi, ENABLE, 10);
			gpio_write(pi, PHASE, 0);
			time_sleep(0.07);
			gpio_write(pi, PHASE, 1);
			time_sleep(0.07);
		}
		else{
			set_PWM_dutycycle(pi, ENABLE, 0);
		}
	}
}

void nfault_cb(int pi, unsigned user_gpio, unsigned edge, uint32_t tick){
	if(edge == FALLING_EDGE){
		printf("nFault turned LOW\n");
		gpio_write(pi, NET_LED, 1);
	}
	else if(edge == RISING_EDGE){
		printf("nFault turned HIGH\n");
		gpio_write(pi, NET_LED, 0);
	}
	else{
		printf("some wierd timeout occured\n");
	}
}

void button_cb(int pi, unsigned user_gpio, unsigned edge, uint32_t tick){
	if(edge == RISING_EDGE){
		gpio_write(pi, GPS_LED, 1);
		shaking=true;
		printf("Button pressed\n");
	}
	else if(edge == FALLING_EDGE){
		gpio_write(pi, GPS_LED, 0);
		shaking=false;
		printf("Button released\n");
	}
}

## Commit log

2024-04-14 Added the example Repo for the berry IMUv4
2024-04-14 Added folder with the relvant berry IMUv4 examples
2024-04-14 Added a setup guide for the rocketpi (Raspberry Pi Zero W / 2W)
2024-04-20 added the kiCad schematics
    [controlPanel.csv, controlPanel.kicad_pcb, controlPanel.kicad_sch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]
2024-05-04 fixed some bugs at the pigpioTest programm
    [pigpioTest.c]
2024-05-09 added a test programm for the modified servo motors and changed spaces to tabs
2024-05-14 changed the footprint of the connector to the controlPanel and changed the order of the pin numbers
    [controlPanel.kicad_pcb, controlPanel.kicad_sch, powerBoard.kicad_pcb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]
2024-05-14 added a test programm for the leds on the controlPanel
2024-05-14 added a test programm for the button
2024-05-16 improved the servo test programm
2024-05-18 fixed some bugs in the servoTest.c program
    [servoTest.c]
2024-05-18 improved the ledTest.c programm
2024-05-18 fixed the button test programm
    [buttonTest.c]
2024-05-18 added a programm to test the servos controlled with the button
2024-05-25 fixed some bugs in the mpu6050 test programm
    [mpu6050Test.c]
2024-05-25 added a test program to make the servos shaking ;)
2024-05-25 added instuctions to config the boot led
2024-05-25 removed berry imu test examples
2024-05-26 fixed some small bugs in rocketpi.c
    [rocketpi.c]
2024-05-31 fixed some small bugs
    [mpu6050Test.c]
2024-05-31 fixed some bug at saving the file
    [mpu6050Test.c]
2024-06-01 tried to fix some bugs
    [rocketpi.c]
